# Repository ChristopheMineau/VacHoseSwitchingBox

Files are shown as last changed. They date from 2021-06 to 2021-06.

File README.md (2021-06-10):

# VacHoseSwitchingBox
A Shop Vacuum Hub Box capable of switching the central shop vac hose to 3 possible machine ports. 
Arduino based control with remote control.

This repo gathers the design files and arduino software for the project.
This project is a complement to the Shop Cyclone project that can be seen here https://github.com/ChristopheMineau/CycloneTurbine

The project is made of a wooden box which is the actual Hub on one side, and a remotely wall mounted plastic control box, which contains a PCB, an arduino board and a few additional components (micro-switches, leds, resistors and a transistor). The two boxes are connected one to the other using a telphone 8 conductors cable.

The command box is powered using a reclaimed 12V DC power supply plug. 

The Cyclone Turbine project uses a remote control, and I decided to use the same remote control, which had plenty of leftover buttons available to control this Hose hub.

The Hub is on one side connected to the Cyclone and to the other side connected to three possible machines or shop stands. 
For instance, in my case :
* One port is permanently connected to the table saw,
* An other to the big band saw,
* And the third one to a 5m flying hose for any use around the shop.

I just have to press buttons P1 / P2 / P3 on the remote control and wait for a few seconds that the desired port is connected to the vacuum.
As an alternative, I can press a faceplate button as well to switch between the ports.
Three leds indicate the current position, and they alternately blink when travelling.
An error condition would be indicated by the three leds blinking at the same time.

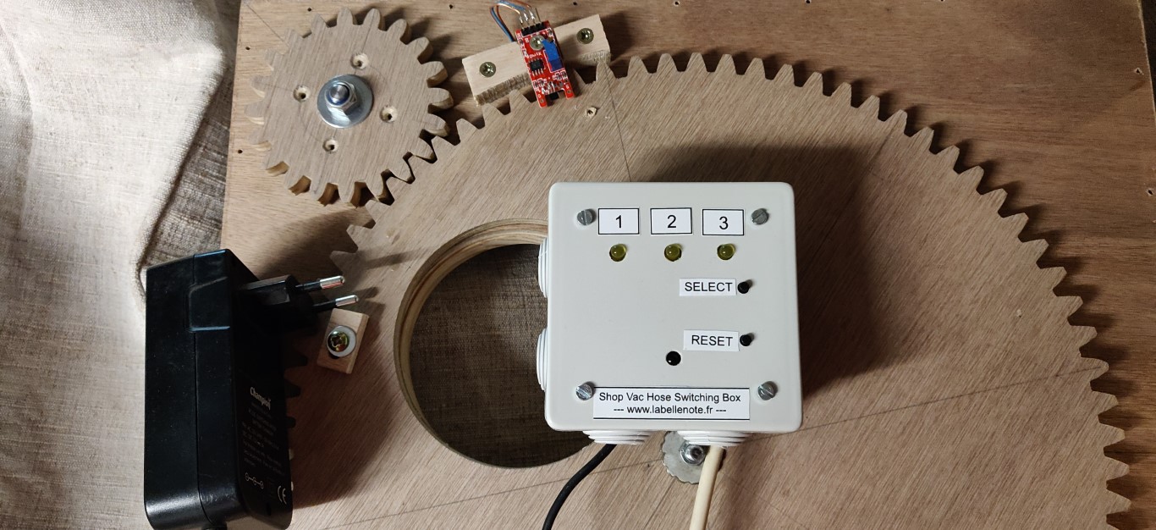
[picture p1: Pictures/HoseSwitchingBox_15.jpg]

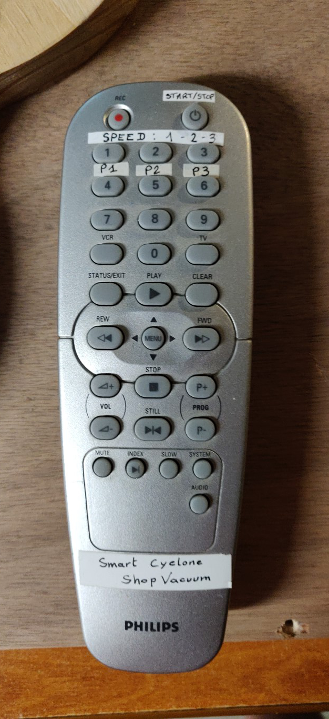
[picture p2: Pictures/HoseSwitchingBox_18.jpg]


## Contents

### Box design folder
The mechanism is based on a large wooden geared crown which acts as an obturator, with a hole allowing to open only one of the three ports.

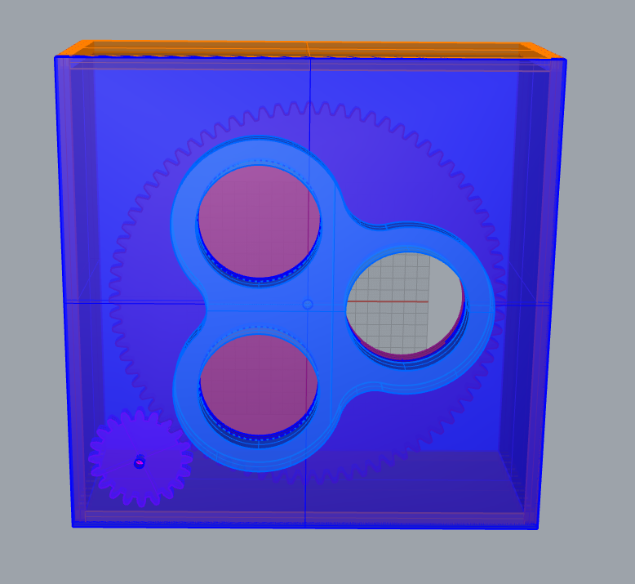
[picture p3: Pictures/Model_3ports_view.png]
Model output ports view

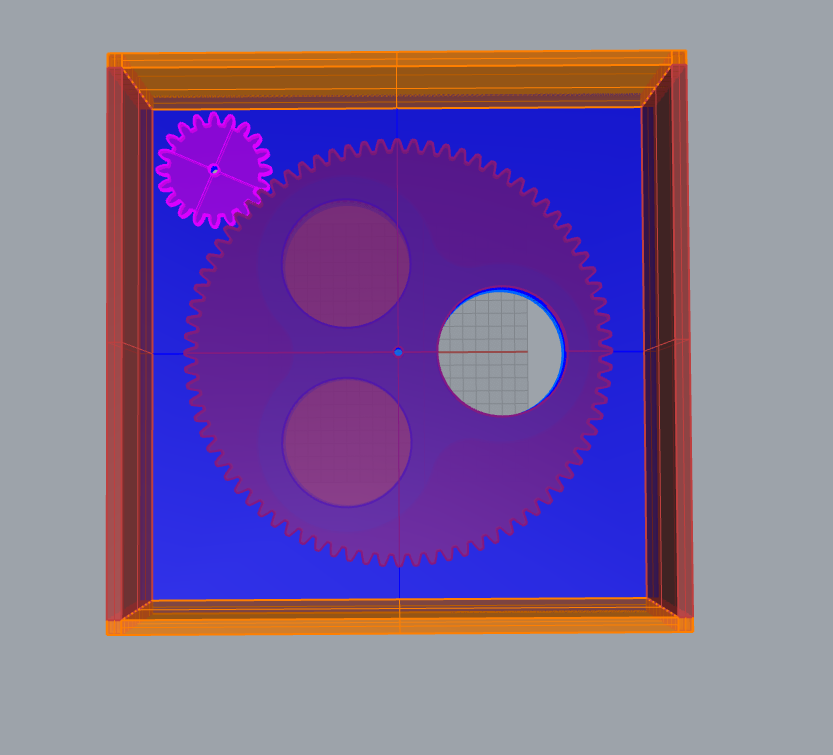
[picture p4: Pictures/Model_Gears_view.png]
Model gears view


There is a small gear which is motored using a small high tork 12V DC motor running at 30 RPM. (Model JGY-371).
This particular model has got a digital encoder in order to locate the exact position of the obturator.
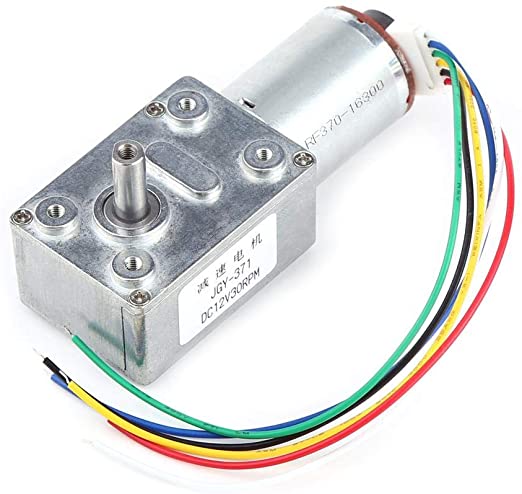
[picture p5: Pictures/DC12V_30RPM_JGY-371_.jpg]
Motor


A reference position is provided by a Hall effect sensor visible on the first picture above. 
A 5mm cylindrical neodimium magnet is inlaid in a small wooden block screwed to the big crown in order to trigger the Hall effect sensor once per revolution.

#### 3dm file
The design is modeled using Rhino 3D.
See https://github.com/ChristopheMineau/VacHoseSwitchingBox/blob/master/Commutateur_tuyaux.3dm

#### Labels
The control board is fitted in an electric box enclosure. The buttons and leds are labelled using stickers designed with this Scribus file.
https://github.com/ChristopheMineau/VacHoseSwitchingBox/blob/master/Scibus_labels.sla
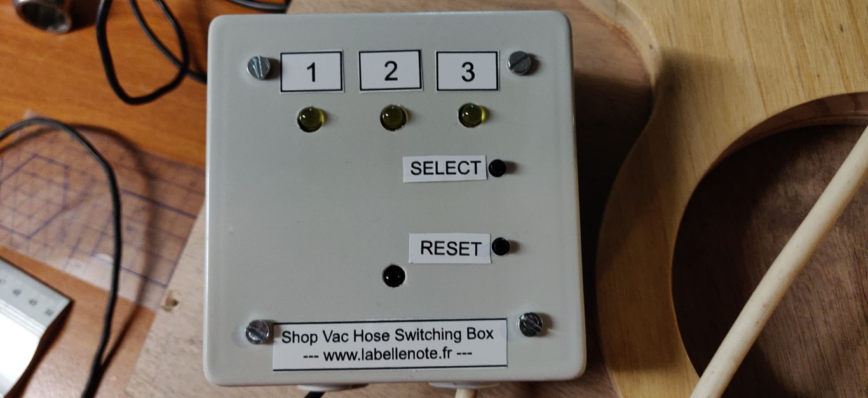
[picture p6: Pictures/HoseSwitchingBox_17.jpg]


#### Gcode folder
This folder contains the gcode to cut the wooden gears with a CNC. As my Cnc bed is too small for cutting the full size crown, I have divided this task into 4 segments and rotated the cut part three times.
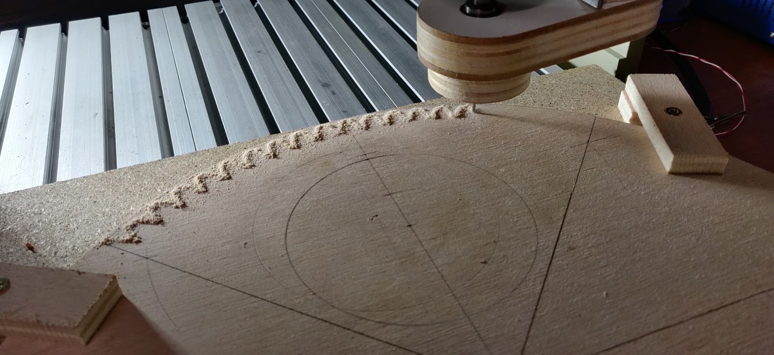
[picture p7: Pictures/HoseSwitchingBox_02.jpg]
Gear cutting 1

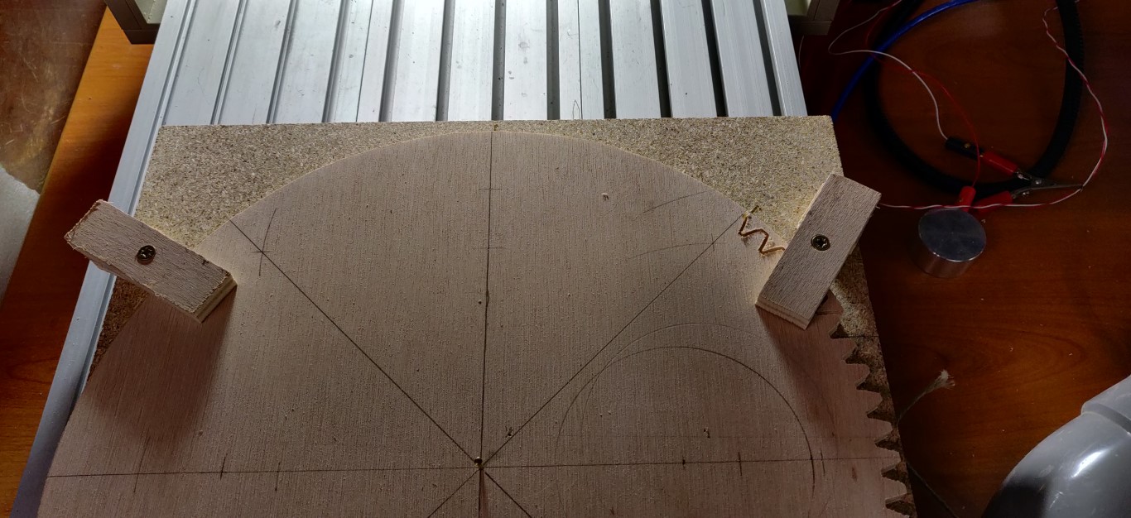
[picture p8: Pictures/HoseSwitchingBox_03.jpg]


### Firmware folder
This is the Arduino code, I used an Arduino Nano like board.
Beware this project is not built using the standard Arduino IDE, but using Visual Studio Code and the PlatformIO extension. (see the numerous tutorials on the Web about that)

### PCB folder
This folder contains the fritzing file with the board schematics and PCB design.
The folder contains also the gerber generated files, the Flatcam project files and as a result the gcode in order to mill this PCB on the cnc.
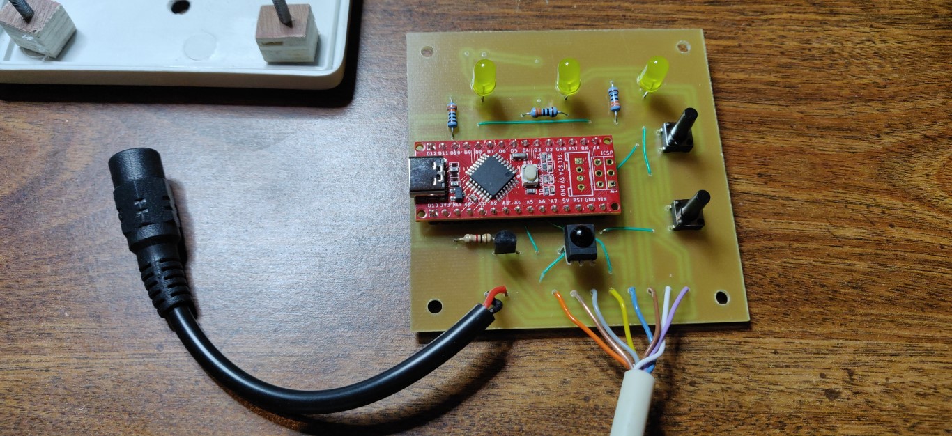
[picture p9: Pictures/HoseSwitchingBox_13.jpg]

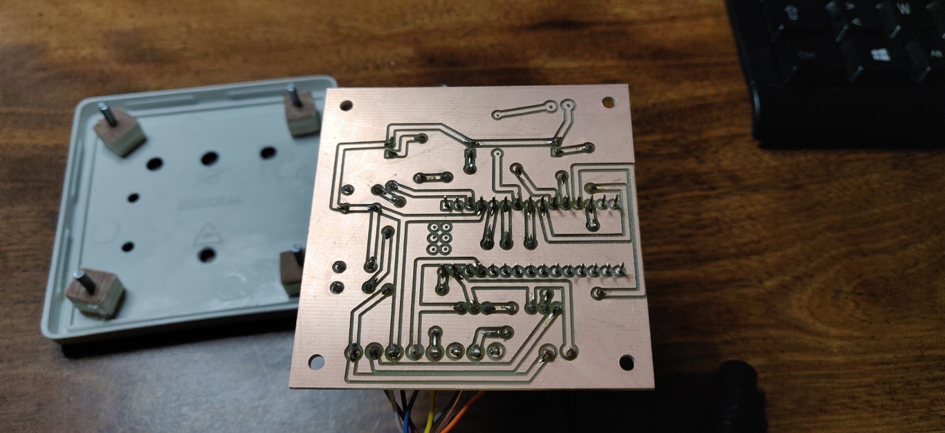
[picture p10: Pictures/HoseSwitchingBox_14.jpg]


### Spec file
See file https://github.com/ChristopheMineau/VacHoseSwitchingBox/blob/master/Spec_connections.TXT

It contains the Arduino pins used for this project and the cabling informations.

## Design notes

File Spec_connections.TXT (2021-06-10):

Connections to Arduino :
================

Position Sensor Hall effect : D2
Encoder A : D3
IR emiter : D4 (provision)
IR receiver : D5
LED1 : D6
LED2 : D7
LED3 : D8
Motor : D9
Button : D10 (pullup)

Cable from command board to switching box ( telephone 8 conductors cable)
-----------------------------------------------------------------------------
Moteur +(12V 400mA) : purple
Moteur -(12V 400mA) : white
GND TTL : brown
VCC TTL 5V : blue
Encodeur A : yellow
Encodeur B : grey
Position Sensor Hall effect : translucid

Codes remote control PHILIPS VCR
==============================
Measures using  D:\Documents\Christophe\Arduino\IR_telecommande\IR_telecommande.ino

Already used for cyclone :
------------------------------
Button start stop :
Protocol=RC5 Address=0x0 Command=0xC Toggle=1 Raw-Data=0x180C 13 bits MSB first
Button 1:
Protocol=RC5 Address=0x0 Command=0x1 Repeat gap=89200us Raw-Data=0x1001 13 bits MSB first
Button 2 : 
Protocol=RC5 Address=0x0 Command=0x2 Toggle=1 Repeat gap=90000us Raw-Data=0x1802 13 bits MSB first
Button 3 :
Protocol=RC5 Address=0x0 Command=0x3 Toggle=1 Raw-Data=0x1803 13 bits MSB first

For the switching box command :
----------------------------------
Button 4 :
Protocol=RC5 Address=0x0 Command=------------------ Raw-Data=0x1004 13 bits MSB first
Button 5 :
Protocol=RC5 Address=0x0 Command=0x5 Toggle=1 Raw-Data=0x1805 13 bits MSB first
Button 6 :
Protocol=RC5 Address=0x0 Command=0x6 Raw-Data=0x1006 13 bits MSB first

Pour l'assainisseur d'air: (provision, non realisé)
--------------------------
STOP pour OFF :
Protocol=RC5 Address=0x0 Command=0x1D Toggle=1 Raw-Data=0x181D 13 bits MSB first
Bouton VOL+ pour ON/SPEED :
Protocol=RC5 Address=0x0 Command=0x10 Raw-Data=0x1010 13 bits MSB first
Bouton P+ pour TIMER :
Protocol=RC5 Address=0x0 Command=0x20 Toggle=1 Raw-Data=0x1820 13 bits MSB first

Codes assainisseur d'air original :
===================================
IRremote ne reconnait pas le protocole.

OFF:
Protocol=UNKNOWN Hash=0xA32AB931 12 bits received
rawData[24]: 
     -1704150
     +1300,- 400     +1300,- 400     + 450,-1200     +1300,- 400
     +1250,- 400     + 450,-1250     + 400,-1250     + 450,-1200
     + 450,-1250     + 450,-1200     + 450,-1250     +1250

TIMER:
Protocol=UNKNOWN Hash=0xE0984BB6 12 bits received
rawData[24]: 
     -8150
     +1250,- 450     +1200,- 450     + 400,-1250     +1250,- 450
     +1250,- 400     + 400,-1250     + 450,-1250     + 400,-1300
     +1200,- 450     + 400,-1250     + 400,-1300     + 400

ON/SPEED:
Protocol=UNKNOWN Hash=0x143226DB 12 bits received
rawData[24]: 
     -3276750
     +1250,- 450     +1200,- 450     + 400,-1250     +1250,- 450
     +1200,- 450     + 400,-1300     + 350,-1300     + 400,-1300
     + 350,-1300     + 400,-1250     +1250,- 450     + 350

La Librairie Infrared4Arduino doit être capable de recevoir et émettre n'importe quelle signature.
==================================================================================================
https://github.com/bengtmartensson/Infrared4Arduino

Samples :
touche : OFF
+1250 -500 +1150 -500 +350 -1300 +1200 -500 +1200 -450 +350 -1350 +350 -1300 +350 -1350 +350 -1300 +350 -1300 +350 -1350 +1200 -7250 +1250 -500 +1150 -500 +350 -1300 +1200 -500 +1150 -500 +350 -1350 +350 -1300 +350 -1300 +350 -1350 +350 -1300 +350 -1350 +1150 -7350 +1200 -450 +1200 -500 +350 -1300 +1200 -500 +1150 -500 +350 -1350 +350 -1300 +350 -1300 +350 -1350 +350 -1300 +350 -1350 +1150 -7300 +1250 -450 +1200 -500 +350 -1300 +1200 -500 +1150 -500 +350 -1300 +400 -1300 +350 -1300 +350 -1350 +350 -1300 +350 -1300 +1200 -7350 +1200 -450 +1200 -500 +350 -1300 +1200 -500 +1150 -500 +350 -1300 +350 -1350 +350 -1300 +350 -1350 +350 -1300 +350 -1350 +1150 -7300 +1250 -450 +1200 -500 +350 -1300 +1200 -500 +1150 -500 +350 -1300 +350 -1350 +350 -1300 +350 -1350 +350 -1300 +350 -1350 +1150 -30100

touche TIMER :
+1250 -450 +1200 -450 +400 -1300 +1200 -450 +1250 -450 +350 -1300 +400 -1250 +400 -1300 +1200 -450 +400 -1300 +350 -1300 +400 -8100 +1250 -450 +1200 -450 +400 -1300 +1200 -450 +1250 -450 +350 -1300 +400 -1300 +350 -1300 +1200 -450 +400 -1300 +350 -1300 +350 -8150 +1250 -450 +1200 -450 +350 -1350 +1200 -450 +1200 -450 +400 -1300 +400 -1250 +400 -1300 +1200 -500 +300 -1300 +400 -1300 +350 -8150 +1200 -500 +1200 -450 +350 -1300 +1250 -450 +1200 -450 +400 -1300 +350 -1300 +350 -1350 +1200 -450 +400 -1250 +400 -1300 +350 -8200 +1150 -450 +1200 -500 +350 -1300 +1250 -450 +1200 -450 +400 -1300 +350 -1300 +350 -1300 +1250 -450 +350 -1300 +350 -1350 +350 -8100 +1250 -450 +1250 -450 +350 -1350 +1200 -450 +1200 -450 +400 -1300 +350 -1300 +350 -1300 +1250 -450 +350 -1300 +400 -1300 +350 -30100

touche ON/SPEED :
+1200 -500 +1200 -450 +400 -1300 +1200 -450 +1200 -500 +350 -1300 +350 -1350 +350 -1300 +350 -1300 +400 -1300 +1200 -450 +350 -8150 +1200 -500 +1200 -450 +350 -1350 +1200 -450 +1200 -450 +400 -1300 +350 -1300 +400 -1300 +350 -1300 +350 -1350 +1200 -450 +350 -8150 +1200 -500 +1200 -450 +350 -1300 +1250 -450 +1200 -450 +400 -1300 +350 -1300 +350 -1350 +350 -1300 +350 -1300 +1200 -500 +350 -8150 +1200 -500 +1200 -450 +350 -1300 +1200 -500 +1200 -500 +350 -1300 +350 -1300 +350 -1350 +350 -1300 +350 -1350 +1150 -500 +350 -8150 +1200 -500 +1150 -500 +350 -1300 +1200 -500 +1200 -450 +350 -1350 +350 -1300 +350 -1350 +350 -1300 +350 -1350 +1150 -500 +350 -8150 +1200 -500 +1150 -500 +350 -1300 +1200 -500 +1200 -450 +350 -1350 +350 -1300 +350 -1350 +350 -1300 +350 -1300 +1200 -500 +350 -30100

Poll:
Samples :
touche : OFF
+1272 -448 +1240 -448 +396 -1268 +1264 -444 +1244 -440 +400 -1292 +400 -1280 +408 -1292 +396 -1288 +396 -1288 +408 -1280 +1248 -7348 +1248 -452 +1236 -428 +416 -1284 +1252 -428 +1256 -440 +400 -1288 +408 -1288 +396 -1292 +396 -1284 +404 -1268 +420 -1292 +1240 -7332 +1272 -440 +1244 -444 +396 -1272 +1260 -444 +1244 -448 +400 -1280 +400 -1292 +400 -1292 +396 -1288 +404 -1280 +400 -1292 +1244 -7356 +1244 -440 +1248 -440 +408 -1280 +1248 -432 +1252 -440 +404 -1296 +396 -1288 +396 -1272 +420 -1264 +420 -1292 +396 -1288 +1244 -7308 +1296 -436 +1244 -448 +400 -1292 +1248 -440 +1240 -436 +404 -1288 +404 -1288 +396 -1288 +400 -1292 +400 -1292 +396 -1288 +1244 -7348 +1248 -448 +1240 -440 +404 -1288 +1244 -440 +1248 -440 +408 -1280 +400 -1292 +400 -1280 +408 -1288 +396 -1288 +404 -1288 +1244 -30008
autre :
+1264 -448 +1244 -436 +408 -1288 +1244 -428 +1260 -436 +404 -1296 +396 -1288 +396 -1268 +424 -1288 +396 -1288 +404 -1264 +1272 -7328 +1268 -444 +1244 -440 +400 -1292 +1244 -444 +1244 -436 +404 -1288 +404 -1264 +424 -1288 +396 -1288 +404 -1264 +424 -1288 +1244 -7336 +1268 -416 +1268 -440 +404 -1276 +1256 -448 +1244 -424 +416 -1284 +404 -1288 +396 -1292 +400 -1288 +400 -1272 +420 -1280 +1248 -7328 +1268 -448 +1244 -452 +392 -1288 +1244 -444 +1244 -440 +400 -1292 +396 -1296 +396 -1288 +396 -1292 +400 -1288 +400 -1292 +1240 -7332 +1268 -436 +1252 -440 +408 -1284 +1244 -440 +1248 -440 +400 -1268 +420 -1292 +392 -1292 +400 -1288 +400 -1272 +416 -1288 +1244 -7328 +1276 -424 +1260 -448 +396 -1288 +1244 -444 +1244 -448 +392 -1292 +400 -1280 +408 -1292 +396 -1268 +416 -1284 +408 -1292 +1236 -7340 +1260 -452 +1236 -448 +396 -1288 +1248 -440 +1248 -440 +400 -1288 +400 -1292 +396 -1288 +404 -1284 +404 -1288 +396 -1292 +1240 -7312 +1284 -432 +1260 -444 +396 -1292 +1244 -444 +1244 -444 +396 -1292 +396 -1288 +404 -1284 +404 -1288 +396 -1288 +404 -1280 +1248 -30012

touche TIMER :
+1268 -440 +1240 -448 +400 -1288 +1244 -448 +1244 -436 +408 -1284 +404 -1268 +416 -1280 +1248 -448 +404 -1280 +408 -1280 +400 -8200 +1244 -444 +1244 -440 +400 -1292 +1244 -424 +1260 -432 +412 -1292 +400 -1288 +400 -1292 +1236 -448 +396 -1288 +400 -1292 +396 -8180 +1268 -420 +1268 -436 +404 -1284 +1244 -452 +1240 -448 +396 -1284 +404 -1288 +396 -1292 +1240 -448 +396 -1268 +420 -1292 +396 -8180 +1260 -444 +1244 -448 +400 -1280 +1248 -448 +1244 -436 +404 -1288 +396 -1276 +416 -1288 +1244 -440 +400 -1288 +400 -1292 +396 -30008
autre 
+1304 -400 +1284 -408 +412 -1272 +1260 -432 +1252 -436 +436 -1280 +408 -1248 +432 -1276 +1256 -412 +436 -1280 +408 -1256 +428 -8172 +1272 -416 +1276 -436 +408 -1292 +1236 -456 +1232 -456 +392 -1280 +408 -1256 +432 -1252 +1280 -436 +408 -1284 +404 -1260 +424 -8172 +1280 -400 +1292 -396 +444 -1252 +1284 -420 +1276 -416 +424 -1260 +428 -1240 +452 -1240 +1288 -396 +448 -1240 +452 -1236 +452 -8120 +1316 -396 +1292 -400 +444 -1240 +1296 -396 +1284 -400 +444 -1260 +428 -1248 +444 -1240 +1292 -412 +408 -1284 +404 -1280 +408 -30008

touche ON/SPEED :
+1264 -436 +1248 -432 +412 -1272 +1260 -424 +1264 -428 +416 -1288 +404 -1276 +408 -1268 +424 -1268 +416 -1268 +1264 -428 +420 -8172 +1268 -420 +1268 -428 +420 -1268 +1264 -420 +1268 -424 +412 -1272 +420 -1272 +412 -1268 +424 -1272 +416 -1268 +1264 -424 +420 -8160 +1280 -424 +1264 -428 +416 -1268 +1264 -424 +1264 -428 +420 -1268 +416 -1268 +420 -1268 +420 -1272 +412 -1280 +1252 -432 +412 -8160 +1288 -428 +1256 -424 +424 -1268 +1264 -428 +1260 -428 +412 -1272 +420 -1268 +416 -1276 +416 -1268 +416 -1268 +1264 -424 +420 -8180 +1264 -424 +1260 -432 +420 -1268 +1264 -424 +1264 -416 +424 -1268 +420 -1268 +420 -1268 +416 -1272 +420 -1264 +1268 -420 +420 -8160 +1288 -420 +1268 -424 +420 -1268 +1260 -428 +1264 -424 +416 -1268 +420 -1272 +420 -1260 +428 -1268 +416 -1268 +1264 -424 +420 -8172 +1268 -424 +1268 -420 +420 -1268 +1264 -424 +1264 -440 +408 -1268 +416 -1264 +420 -1272 +420 -1280 +408 -1268 +1260 -428 +416 -8160 +1288 -420 +1264 -420 +420 -1268 +1268 -420 +1268 -436 +408 -1284 +404 -1268 +416 -1268 +420 -1272 +420 -1272 +1260 -424 +416 -30016
autre
+1228 -460 +1232 -464 +380 -1308 +1224 -460 +1232 -452 +392 -1280 +408 -1300 +384 -1304 +384 -1300 +388 -1300 +1232 -464 +380 -8208 +1236 -456 +1232 -460 +380 -1312 +1224 -456 +1232 -456 +384 -1312 +376 -1284 +404 -1308 +380 -1280 +412 -1300 +1232 -460 +384 -8204 +1236 -460 +1224 -456 +388 -1300 +1232 -460 +1232 -452 +392 -1280 +408 -1288 +396 -1308 +384 -1296 +392 -1280 +1248 -456 +388 -8212 +1232 -452 +1232 -460 +384 -1280 +1256 -456 +1228 -392 +456 -1300 +384 -1296 +396 -1300 +384 -1300 +388 -1308 +1224 -460 +388 -8200 +1244 -428 +1256 -416 +424 -1280 +1256 -428 +1256 -416 +428 -1232 +460 -1252 +416 -1276 +412 -1272 +420 -1268 +1296 -396 +444 -8148 +1296 -412 +1276 -408 +436 -1260 +1272 -396 +1292 -412 +432 -1240 +444 -1256 +432 -1240 +448 -1260 +432 -1236 +1292 -400 +444 -30004

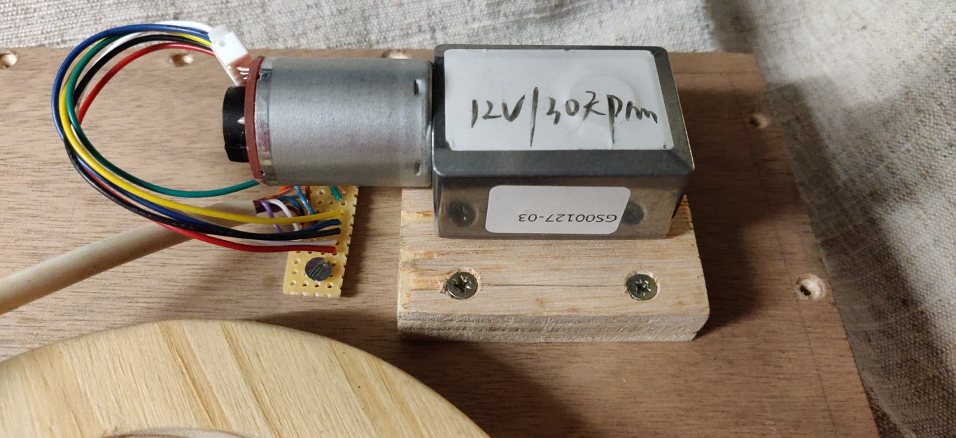
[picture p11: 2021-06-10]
Pictures/HoseSwitchingBox_16.jpg

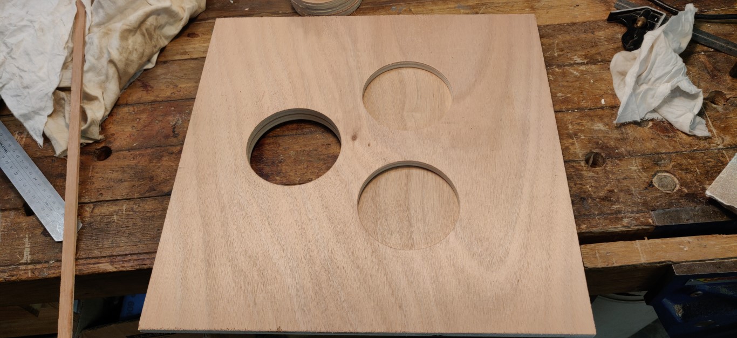
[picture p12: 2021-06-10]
Pictures/HoseSwitchingBox_07.jpg

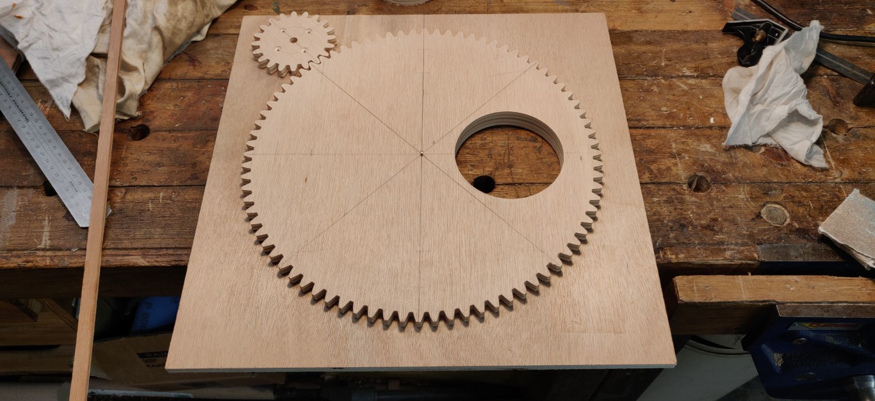
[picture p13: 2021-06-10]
Pictures/HoseSwitchingBox_06.jpg

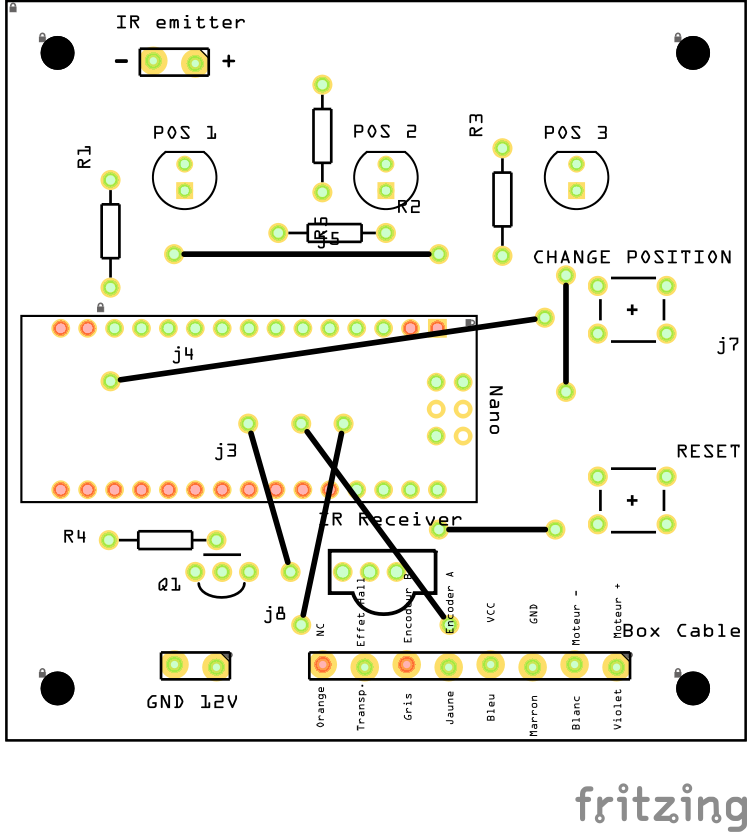
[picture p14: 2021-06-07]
PCB/VacHoseSwitchingBox_PCB_silk front.png

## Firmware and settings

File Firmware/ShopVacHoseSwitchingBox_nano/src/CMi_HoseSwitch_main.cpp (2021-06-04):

#define VERSION "1.0"
#include <Arduino.h>
#include <avr/io.h>
#include <avr/interrupt.h>
#include <util/atomic.h>

#include  "CMi_Constants.h" /// !! Check this file for activating DEBUG prints
#include <IRremote.h>  // https://github.com/Arduino-IRremote/Arduino-IRremote   Version3.1.0
#include  "CMi_Control.h"

// Globals
volatile int encoderPulseCount = 0;    // encoder pulses count variable
volatile int pulseToGo = 0;            // encoder count to be reached
volatile int countBeforeStopping = 0;      // saved encoder count befor stopping
volatile unsigned long postCalibrationTime = 0;  // timer after reaching POS 0 to go to POS1 as initial POS at startup
HoseSwitchControl hoseSwitch = HoseSwitchControl();

// Interrupt Service Routines
void encoderInterrupt() {      // encoder rising edge detected
  encoderPulseCount++;
  if (digitalRead(POS_SENSOR) == HIGH) {
        // To calculate the number of pulses per rev and inertia, reset twice and look at the traces
      if (encoderPulseCount > 100) {   // in order to reset only when we enter the magnetic field
        countBeforeStopping = encoderPulseCount;
        encoderPulseCount = 0; 
        if (pulseToGo == 9999) {     // desired Pos = Pos0 reference point
          hoseSwitch.posReached();
        }
      }
  }

  if ((pulseToGo != 9999) and (hoseSwitch.state == HoseSwitchControl::State::RUNNING)) {     
    pulseToGo --;
    if (pulseToGo == 0) hoseSwitch.posReached();
  }
  
}



///// BEGIN //// SETUP //// SETUP //// SETUP //// SETUP //// SETUP //// SETUP //// SETUP //// SETUP //// SETUP //// SETUP ////
void setup() {

// Just to know which program is running on my Arduino
  Serial.begin(115200);
  Serial.println(F("START " __FILE__ " from " __DATE__ " version " VERSION));

#ifndef DEBUG
  Serial.end();
#endif   // DEBUG

  // Set up pins
  // Input digital pins
  pinMode(SELECT_BUTTON, INPUT_PULLUP); // Select button (INPUT_PULLUP)
  pinMode(POS_SENSOR, INPUT);           // Hall effect POS 0 sensor (active LOW)
  pinMode(ENCODER_A, INPUT);            // Motor digital encoder A
  pinMode(REMOTE_RECEIVER, INPUT);      // IR Remote control receiver

  // Output digital pins
  pinMode(LED_POS_1, OUTPUT);       // set Position indicator led pins
  pinMode(LED_POS_2, OUTPUT);
  pinMode(LED_POS_3, OUTPUT);
  pinMode(REMOTE_SEND, OUTPUT);     // IR Remote control emitter
  pinMode(MOTOR, OUTPUT);           // Motor driver transistor base
 
  // Remote control 
  IrReceiver.begin(REMOTE_RECEIVER, ENABLE_LED_FEEDBACK, USE_DEFAULT_FEEDBACK_LED_PIN);
                                     
  // set up Encoder interrupt IRQ0 on pin 2.
  attachInterrupt(digitalPinToInterrupt(ENCODER_A), encoderInterrupt, RISING); //IRQ 0

  // Init Control object
  hoseSwitch.init();
}
///// END //// SETUP //// SETUP //// SETUP //// SETUP //// SETUP //// SETUP //// SETUP //// SETUP //// SETUP //// SETUP ////





namespace DEBUG_ {
  void displayStatus(bool forceDisplay=false) {
    unsigned  int countCopy;
    unsigned  int pulseToGoCopy;
#ifndef DEBUG                    // See CMi_Constants.h for activating the DEBUG flag
    return;
#endif   // DEBUG
    static unsigned long lastTime = 0;
    if (((millis() - lastTime )> 3000) or forceDisplay) {
      ATOMIC_BLOCK(ATOMIC_RESTORESTATE) {
        countCopy = encoderPulseCount;
        pulseToGoCopy = pulseToGo;
      }
      DEBUG_PRINTLN("");
      DEBUG_PRINT("hoseSwitch state = ");
      DEBUG_PRINTLN(hoseSwitch.state);
      DEBUG_PRINT("desiredPos = ");
      DEBUG_PRINTLN(hoseSwitch.desiredPos); 
      DEBUG_PRINT("currentPos = ");
      DEBUG_PRINTLN(hoseSwitch.currentPos);
      DEBUG_PRINT("encoderCount = ");
      DEBUG_PRINTLN(countCopy);
      DEBUG_PRINT("pulseToGo = ");
      DEBUG_PRINTLN(pulseToGoCopy);
      lastTime = millis();
    }  
  }
}

int checkRemoteControl() {
  int irCode = 0xFF;
  static int currentlyReceivingCode = 0xFF;
  int receivedCode;
  static unsigned long lastIrChangeTime = 0;
  
  if (IrReceiver.decode()) {
    IrReceiver.resume(); // Enable receiving of the next value
    receivedCode = IrReceiver.decodedIRData.command; 
    
    if (receivedCode != currentlyReceivingCode) {           // reject repetitions of the same code
      if ((IrReceiver.decodedIRData.protocol == RC5) and   // Protocol used by the Philips VCR remote control
          ((receivedCode == 0x4) or
            (receivedCode == 0x5) or
            (receivedCode == 0x6))) {
#ifdef DEBUG
          IrReceiver.printIRResultShort(&Serial);  // FOR DEBUG 
          DEBUG_PRINTLN(IrReceiver.decodedIRData.flags);
#endif   // DEBUG

            currentlyReceivingCode = receivedCode;
            irCode = receivedCode;
            lastIrChangeTime = millis();
        }   
    }     
  }
  if (millis() - lastIrChangeTime > DEBOUNCE_TIME)
     currentlyReceivingCode = 0xFF;
  
  return irCode;
}




///// BEGIN //// LOOP //// LOOP //// LOOP //// LOOP //// LOOP //// LOOP //// LOOP //// LOOP //// LOOP //// LOOP ////
void loop() {
  DEBUG_::displayStatus();
  
  // Get the last Faceplate and remote control actions and update the controller
  hoseSwitch.update(checkRemoteControl());
   
  // diagnose a possible fault
  if ((hoseSwitch.state == HoseSwitchControl::State::RUNNING) and hoseSwitch.checkRunningDuration())
    hoseSwitch.stuckError();
}
///// END //// LOOP //// LOOP //// LOOP //// LOOP //// LOOP //// LOOP //// LOOP //// LOOP //// LOOP //// LOOP ////

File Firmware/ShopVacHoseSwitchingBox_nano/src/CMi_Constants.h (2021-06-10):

#ifndef CMI_CONSTANTS_H
#define CMI_CONSTANTS_H

// Pins
#define SELECT_BUTTON    10       // Select button (INPUT_PULLUP)
#define POS_SENSOR       2        // Hall effect POS 0 sensor (active LOW)
#define ENCODER_A        3        // Motor digital encoder A
#define REMOTE_SEND      4        // IR Remote control emitter
#define REMOTE_RECEIVER  5        // IR Remote control receiver

#define LED_POS_1        6
#define LED_POS_2        7
#define LED_POS_3        8
#define MOTOR            9

// Constants
#define ONE_REVOLUTION_COUNT 8400    // Pulse count to turn one full revolution 
                                     // Eval. : reset when on pos1 and check traces POS0 "Encoder before stopping" + POS1_COUNT
#define STOPPING_INERTIA 336         // pulses from inertia after stopping 
                                     //  Eval. : after reset, before moving from POS0 to POS1 "Encoder before moving")
#define POS1_COUNT  1430     // Pulse count to reach POS 1 from POS 0 (determins by try and fail)
#define POS2_COUNT  4220     // Pulse count to reach POS 2 from POS 0  // POS1_COUNT + ONE_REVOLUTION_COUNT/3 
#define POS3_COUNT  7000     // Pulse count to reach POS 3 from POS 0  // POS2_COUNT + ONE_REVOLUTION_COUNT/3 =5600

#define DEBOUNCE_TIME 400  // in millis
#define BLINK_TIME 400     // in millis
#define STUCK_TIME_LIMIT 12000 // running time beyond which the motor is considered as stuck
#define POST_CAIBRATION_DELAY 1000 // time after reaching POS0 to head to POS1

// #define DEBUG   // Activates the debug prints, comment for final version
#ifdef DEBUG
  #define DEBUG_PRINT(...)    Serial.print(__VA_ARGS__)
  #define DEBUG_PRINTLN(...)  Serial.println(__VA_ARGS__)
#else
  #define DEBUG_PRINT(...) void()
  #define DEBUG_PRINTLN(...) void()
#endif //    DEBUG

#endif //    CMI_CONSTANTS_HH

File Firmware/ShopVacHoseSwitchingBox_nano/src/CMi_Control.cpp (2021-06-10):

#include  "CMi_Control.h"

HoseSwitchControl::HoseSwitchControl() : 
        state(State::STOPPED), 
        currentPos(Pos::INTERMEDIATE),
        desiredPos(Pos::POS1),
        pos1Led(Led(LED_POS_1)),
        pos2Led(Led(LED_POS_2)),
        pos3Led(Led(LED_POS_3)),
        selectButton(Button(SELECT_BUTTON)),
        startRunningTime(0) {}

void HoseSwitchControl::init() {
  desiredPos = Pos::POS0;
  goToDesiredPos();
}

void HoseSwitchControl::update(int irCode) {
  inputUpdate(irCode);
  updateDisplay();
}

void HoseSwitchControl::goToDesiredPos(){
  unsigned int countCopy;
  ATOMIC_BLOCK(ATOMIC_RESTORESTATE) {
    countCopy = encoderPulseCount;
  }
  if ((state == State::STOPPED) and (desiredPos != currentPos)) {
    startRunningTime = millis();
    state = State::RUNNING ;
    switch(desiredPos) {
      case(Pos::POS0):
        pulseToGo = 9999;
        break;
      case(Pos::POS1):
        pulseToGo = POS1_COUNT;
        break;
      case(Pos::POS2):
        pulseToGo = POS2_COUNT;
        break;
      case(Pos::POS3):
        pulseToGo = POS3_COUNT;
        break; 
      default:
        break;      
    }
    if (pulseToGo != 9999) {
      if (pulseToGo < countCopy) // We have passed the target, need to add a full turn
        pulseToGo = pulseToGo + ONE_REVOLUTION_COUNT - countCopy - STOPPING_INERTIA;
      else
        pulseToGo = pulseToGo - countCopy - STOPPING_INERTIA;
    }

    digitalWrite(MOTOR, HIGH);
    currentPos = Pos::INTERMEDIATE;
    DEBUG_PRINTLN();
    DEBUG_PRINT("Encoder before moving : ");
    DEBUG_PRINTLN(countCopy); 
    DEBUG_PRINT("Going to Pos : ");
    DEBUG_PRINT(desiredPos);
    DEBUG_PRINT(" Pulse to Go : ");
    DEBUG_PRINTLN(pulseToGo); 
  }
}

void HoseSwitchControl::posReached(){  // beware called by interrupt, once decount reached
  int countCopy;
  digitalWrite(MOTOR, LOW);
  state = State::STOPPED ;             // this will stop the call by interrupt
  ATOMIC_BLOCK(ATOMIC_RESTORESTATE) {
    countCopy = countBeforeStopping;
  }
  DEBUG_PRINTLN();
  DEBUG_PRINT(" ### Reached Pos : ");
  DEBUG_PRINTLN(desiredPos);
  DEBUG_PRINT("Encoder before stopping : ");
  DEBUG_PRINTLN(countCopy);
  if (desiredPos == Pos::POS0) {
    DEBUG_PRINTLN("**** POS 0 (Hall sensor) ***");  
    ATOMIC_BLOCK(ATOMIC_RESTORESTATE) {
      postCalibrationTime = millis();
    }
  }
  currentPos = desiredPos;
}

void HoseSwitchControl::inputUpdate(int irCode) {
  static Pos previousDesiredPos = Pos::POS3;


  // handle post Calibration delay to go to startup POS = 1
  if (postCalibrationTime != 0) {
    if ((millis() - postCalibrationTime) > POST_CAIBRATION_DELAY) {
      desiredPos = Pos::POS1;
      goToDesiredPos();
      postCalibrationTime = 0;
    }
  }

  // handle irCode if any
  if (irCode != 0xFF and state == State::STOPPED) {
    switch (irCode) {
      case 0x4:     //  button 4   on PHILIPS VCR remote control
        desiredPos = Pos::POS1;
        break;
      case 0x5:     //  button 5  on PHILIPS VCR remote control
        desiredPos = Pos::POS2;
        break;
      case 0x6:     //  button 6  on PHILIPS VCR remote control
        desiredPos = Pos::POS3;
        break;
    }
    goToDesiredPos();
  }   
  
  // handle faceplate button
  if (selectButton.getState() and state == State::STOPPED) {
    DEBUG_PRINTLN();
    DEBUG_PRINTLN("Switch button Hit.");
    switch(previousDesiredPos) {
      case(Pos::POS1):
        desiredPos = Pos::POS2;
        break;
        
      case(Pos::POS2):
        desiredPos = Pos::POS3;
        break;
        
      case(Pos::POS3):
        desiredPos = Pos::POS1;   
        break;

      default:
        break;
    }
    previousDesiredPos = desiredPos;
    goToDesiredPos();   
  } 
  
}

void HoseSwitchControl::updateDisplay() {

  switch(state) {
    case(State::STOPPED):
      
      switch(currentPos) {
        case(Pos::POS0):
          pos1Led.reset();
          pos2Led.reset();
          pos3Led.reset();
          break;
        case(Pos::POS1):
          pos1Led.set();
          pos2Led.reset();
          pos3Led.reset();
          break;
        case(Pos::POS2):
          pos1Led.reset();
          pos2Led.set();
          pos3Led.reset();
          break;
        case(Pos::POS3):
          pos1Led.reset();
          pos2Led.reset();
          pos3Led.set();
          break;
        default:
          break;
      }
      break;
    
    case(State::RUNNING):
      roundRobin(pos1Led, pos2Led, pos3Led);
      break;
      
    case(State::STALLED):
      synchBlink(pos1Led, pos2Led, pos3Led);
      break;
  }
  
  pos1Led.update();
  pos2Led.update();
  pos3Led.update();
}

void HoseSwitchControl::roundRobin(Led& l1, Led& l2, Led& l3) {
  static unsigned long lastBlinkTime = 0;
  static byte lastBlinkLed = 4;

  if ((millis()-lastBlinkTime)>BLINK_TIME) {
    switch(lastBlinkLed) {
      case(1):
          l1.reset();
          l2.set();
          l3.reset();
          lastBlinkLed = 2;
          break;
      case(2):
          l1.reset();
          l2.reset();
          l3.set();
          lastBlinkLed = 3;
          break;
      case(3):
          l1.reset();
          l2.set();
          l3.reset();
          lastBlinkLed = 4;
          break; 
      case(4):
          l1.set();
          l2.reset();
          l3.reset();
          lastBlinkLed = 1;
          break;             
    }
    lastBlinkTime = millis();
  }
}

void HoseSwitchControl::synchBlink(Led& l1, Led& l2, Led& l3) {
  static unsigned long lastBlinkTime = 0;
  if (not lastBlinkTime) {
    l1.set();
    l2.set();
    l3.set();
  }
  if ((millis()-lastBlinkTime)>BLINK_TIME) {
    l1.toggle();
    l2.toggle();
    l3.toggle();
    lastBlinkTime = millis();
  }
}

bool HoseSwitchControl::checkRunningDuration() {
  if (state != State::RUNNING) return false;
  if ((millis() - startRunningTime) > STUCK_TIME_LIMIT) return true;
  return false;
}


// Error Handler
void HoseSwitchControl::stuckError() {   //  0 Pos is not reached
  DEBUG_PRINTLN("### Stuck Error. Motor does not turn or Hall effect sensor down ...");
  state = HoseSwitchControl::State::STALLED;
  digitalWrite(MOTOR, LOW);
  DEBUG_::displayStatus(true);
  while (1) {                  // Dead end ...
    updateDisplay();
    delay(100);
  } 
}

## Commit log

2021-06-03 fix button issue
2021-06-03 Fix Button Pin 1 interaction with Serial
    [CMi_Constants.h, CMi_Control.cpp]
2021-06-07 Add PCB Fritzing and Flatcam files
    [VacHoseSwitchingBox_PCB.fzz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]
2021-06-08 Final version V1.0 refactored for Nano board and removed debug traces
2021-06-10 add motor picture
